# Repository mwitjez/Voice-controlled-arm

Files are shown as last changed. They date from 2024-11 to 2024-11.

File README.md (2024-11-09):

# Voice-Controlled Robotic Arm 🦾

## Project Overview

This project involves designing and constructing a robotic arm controlled via voice commands, utilizing Amazon Alexa for voice recognition. It explores key areas in robotics, including mechanical arm construction, voice control systems, and integration with various electronic components for seamless functionality. The goal is to create an intuitive robotic interface that allows users to interact naturally with the robot through simple commands.

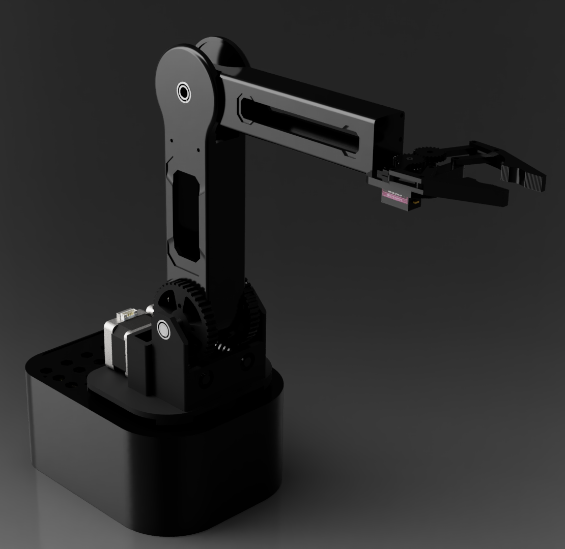
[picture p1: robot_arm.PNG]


## Table of Contents
- [Project Overview](#project-overview)
- [Project Objectives](#project-objectives)
- [Features](#features)
- [Technologies Used](#technologies-used)
- [System Architecture](#system-architecture)
- [Setup Instructions](#setup-instructions)
- [Usage](#usage)
- [Acknowledgments](#acknowledgments)

## Features

- **Voice Control**: The robotic arm can be controlled with voice commands, powered by Amazon Alexa.
- **Digital Control System**: Includes a custom PCB with an Arduino Nano and motor drivers to control stepper motors for precise movement.
- **Vision System**: Integrates a Microsoft Kinect camera for object detection and environmental awareness.
- **3D-Printed Components**: Many mechanical parts are 3D-printed, providing flexibility and accessibility in design.

## Technologies Used

- **Mechanical Design**: Autodesk Fusion 360, 3D Printing (PLA filament)
- **Electronics**: Arduino Nano, Raspberry Pi, TMC2130 Motor Drivers, Mean Well EDR-120-12 Power Supply
- **Programming Languages**: Python (for Raspberry Pi), C++ (for Arduino Nano)
- **Voice Assistant**: Amazon Alexa and AWS Lambda for command processing
- **Communication Protocols**: MQTT for communication between Raspberry Pi and Alexa's cloud services

## System Architecture

The system architecture consists of:
- **Voice Control Module**: Amazon Alexa interprets commands and communicates with the Raspberry Pi via AWS Lambda and MQTT.
- **Electronic Control Module**: A Raspberry Pi processes commands and interfaces with the Arduino Nano to control motors and the camera.
- **Mechanical Control Module**: Includes stepper motors and servo-based grippers for precise control of the robotic arm.

## Setup Instructions

### Project structure

```
.
├── 3D printed parts/   # 3D models for printed parts
├── code/               # Main application code
└── PCB/                # PCB design files
```

1. **Hardware Assembly**:
   - Assemble 3D-printed and off-the-shelf components, following the assembly guide.
   - Connect motors, camera, and power supply to the Raspberry Pi and Arduino Nano.
   
2. **Software Installation**:
   - Install the required Python libraries on Raspberry Pi for voice processing and motor control.
   - Set up the Arduino Nano with the control code for managing motor functions.
   - Configure the Alexa Skill with AWS Lambda function and enable MQTT for command messaging.

3. **Voice Command Setup**:
   - Configure the Alexa Skill for the robotic arm using the Alexa Skills Kit (ASK).
   - Link Alexa to the AWS IoT Core via MQTT for seamless communication.

## Usage

After setup, activate the Alexa skill with the command phrase `"Wake up, samurai"`, and use the following commands to control the robotic arm:
- **"Open the gripper"** or **"Close the gripper"**
- **"Move [direction] [distance]"** (e.g., "Move forward 5 centimeters")
- **"Rotate [direction] [angle]"** (e.g., "Rotate left 30 degrees")
- **"Pick it up"** - Grasp an object using the gripper
- **"Stop moving"** - Stop all movements

## Acknowledgments

This project was developed as part of an Engineering Thesis at Gdańsk University of Technology. All rights are reserved by the university.

Please note that the code and associated files for this project have not been updated and may be in an incomplete or outdated state. This project was initially developed four years ago, at a time when I had limited experience with the technologies and concepts involved. As a result, the structure and implementation may not reflect best practices or current standards. While the project serves as a foundation, it is recommended to consider it as a learning artifact rather than a fully polished, production-ready solution.

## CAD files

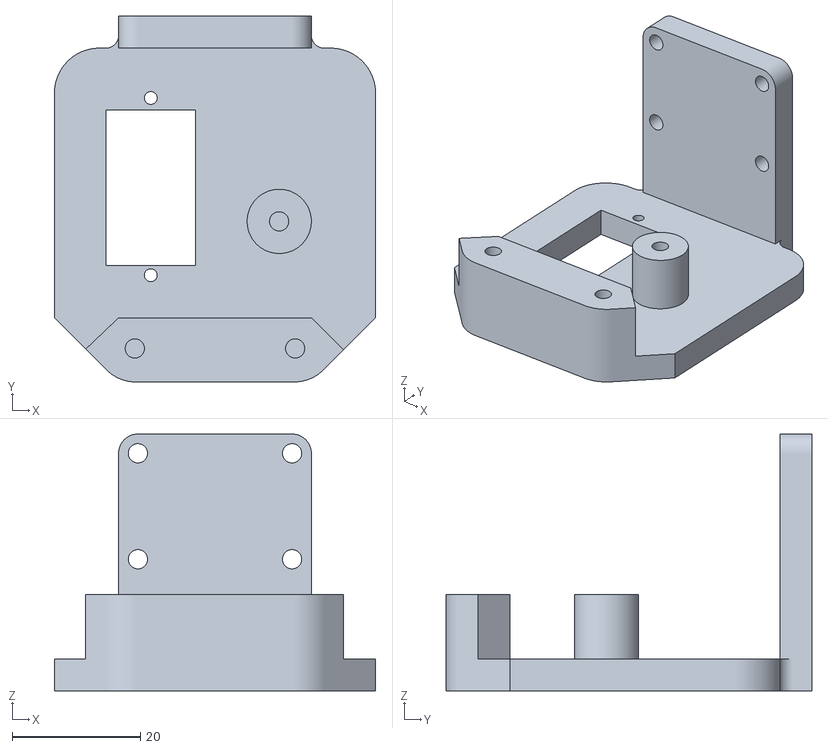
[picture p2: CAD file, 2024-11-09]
3D printed parts/Gripper base.stl
50.0 x 57.0 x 40.0

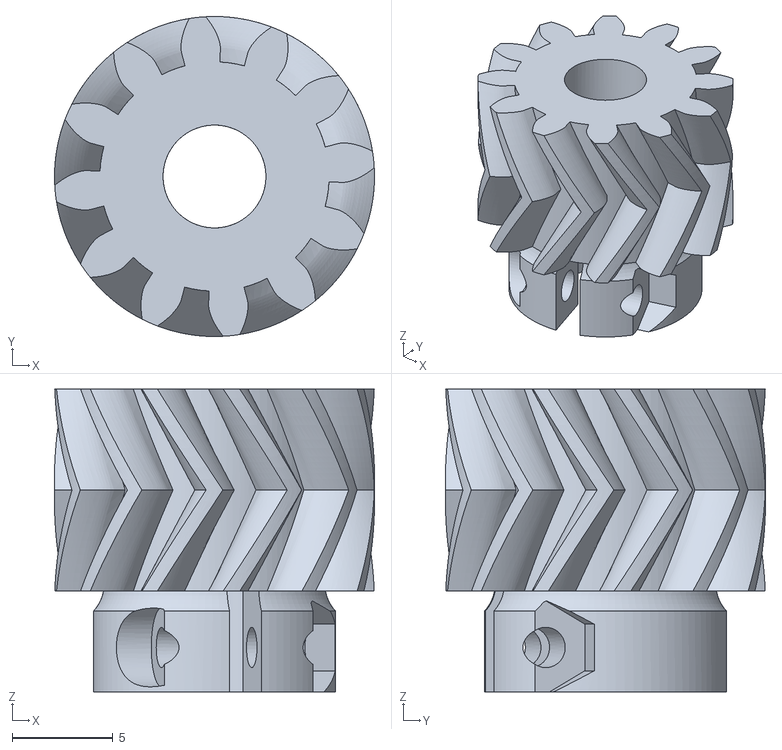
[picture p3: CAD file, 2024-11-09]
3D printed parts/Healical Gear base.stl
15.9 x 15.9 x 15.0

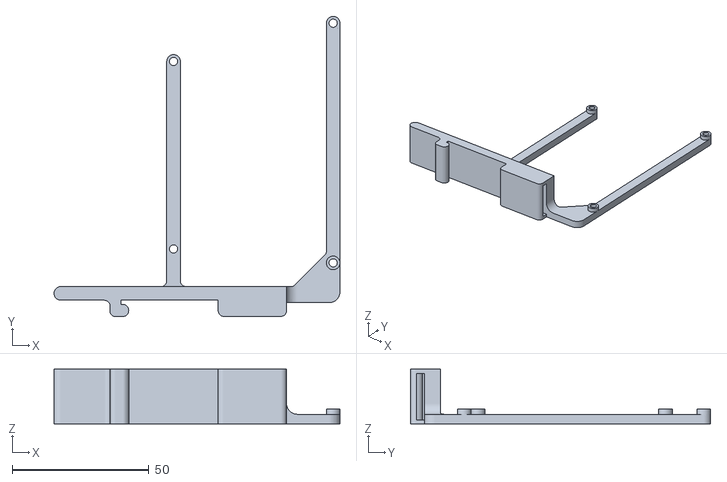
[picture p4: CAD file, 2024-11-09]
3D printed parts/PCB DIN mount.stl
104.5 x 109.7 x 20.0

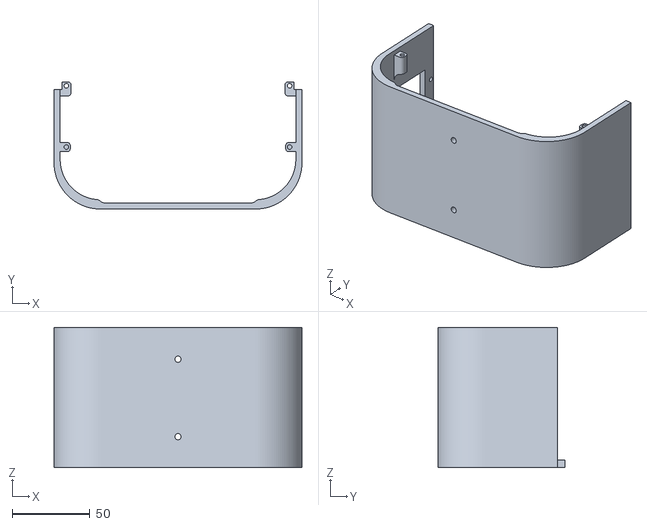
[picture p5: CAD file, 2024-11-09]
3D printed parts/Case back.stl
160.0 x 82.0 x 90.6

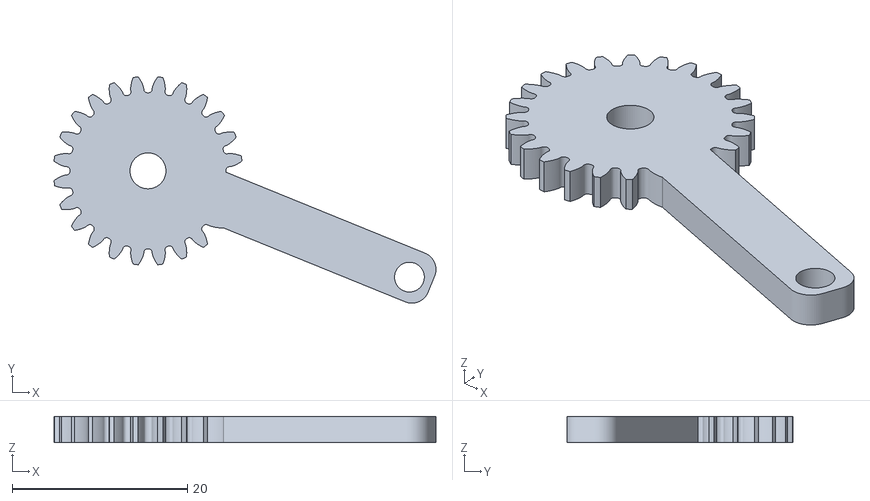
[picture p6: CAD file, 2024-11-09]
3D printed parts/gripper gear right.stl
43.6 x 25.8 x 3.00

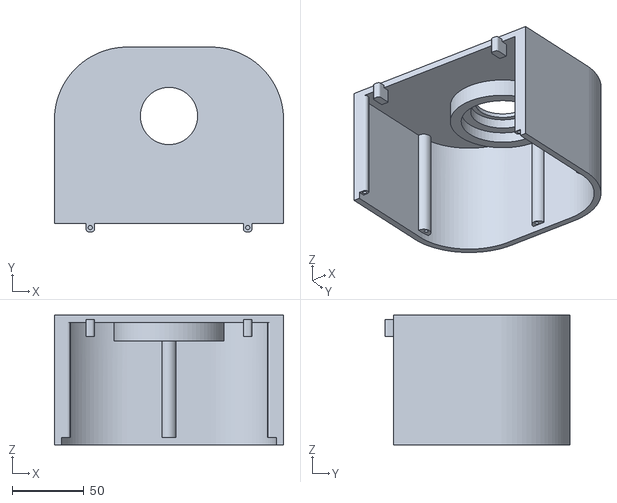
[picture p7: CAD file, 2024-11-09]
3D printed parts/Case front.stl
160.0 x 129.1 x 90.6

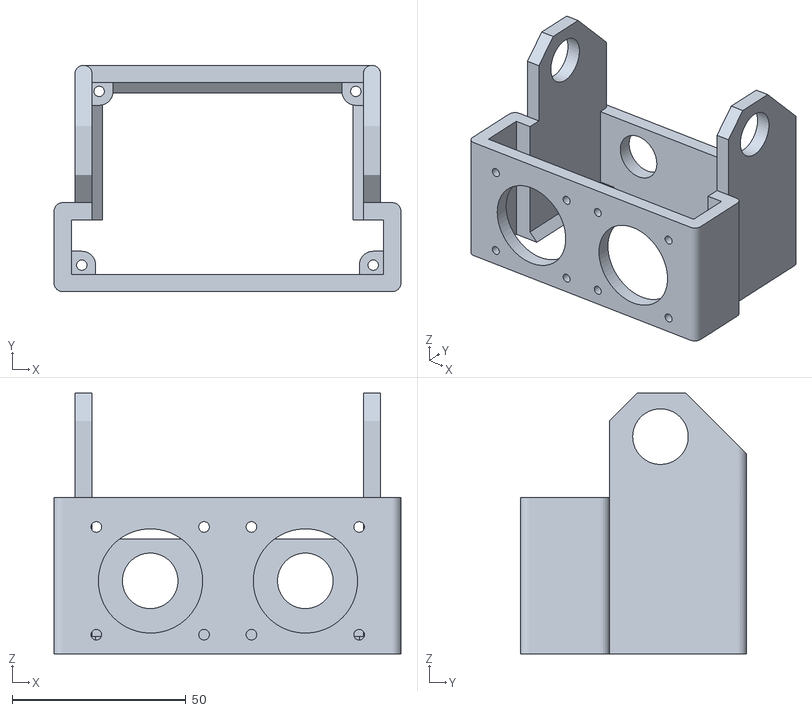
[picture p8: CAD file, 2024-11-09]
3D printed parts/Base upper.stl
99.9 x 65.1 x 75.0

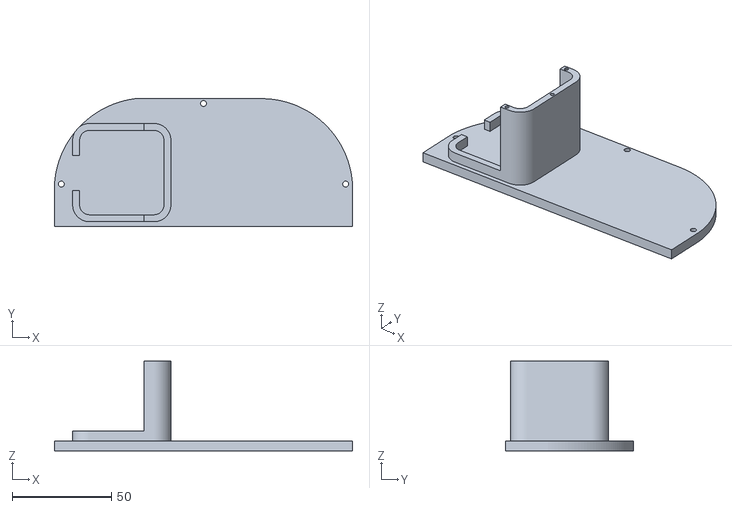
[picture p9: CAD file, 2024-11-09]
3D printed parts/Case lower.stl
149.8 x 64.2 x 45.0

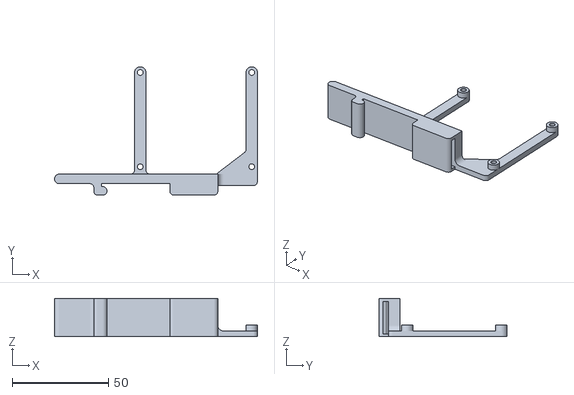
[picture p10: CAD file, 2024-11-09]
3D printed parts/rPi DIN mount.stl
105.6 x 66.8 x 20.0

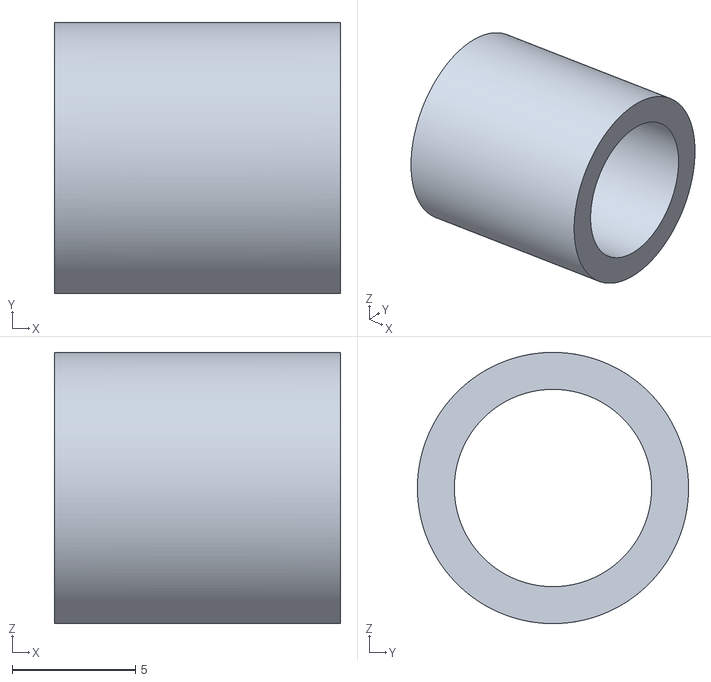
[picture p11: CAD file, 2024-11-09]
3D printed parts/spacer.stl
11.6 x 11.0 x 11.0

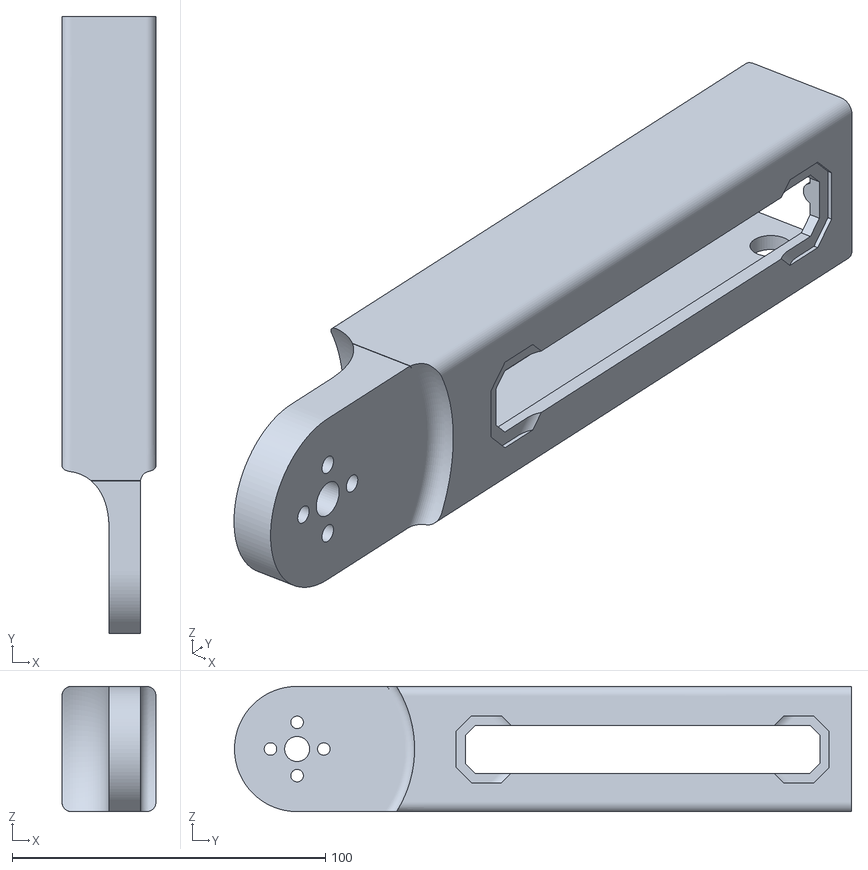
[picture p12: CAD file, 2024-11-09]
3D printed parts/Arm upper.stl
30.0 x 197.0 x 40.0

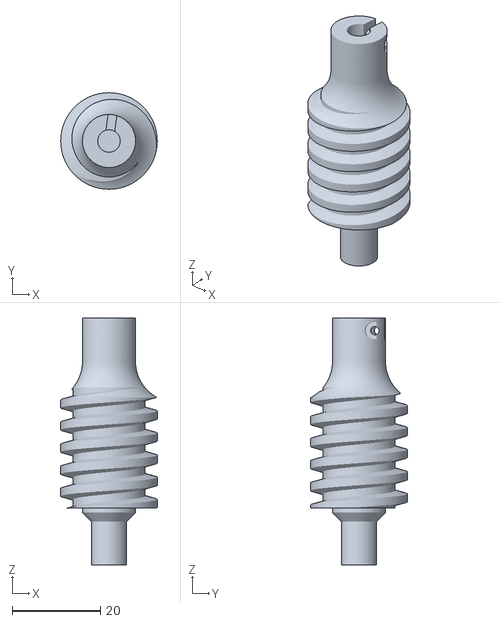
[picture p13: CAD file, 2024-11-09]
3D printed parts/worm upper fixed.stl
21.8 x 21.8 x 55.9

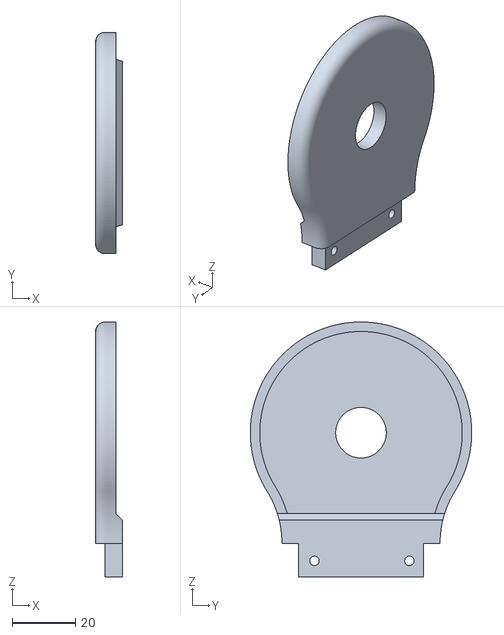
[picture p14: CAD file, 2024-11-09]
3D printed parts/Joint 2 connector.stl
8.50 x 70.0 x 80.6

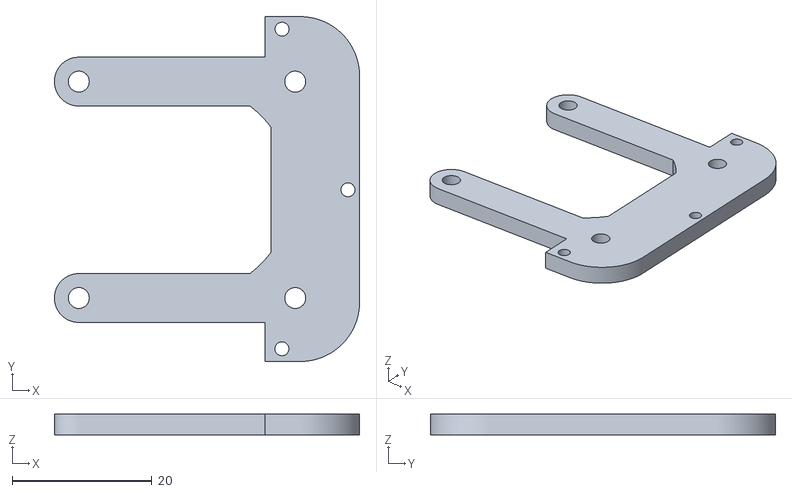
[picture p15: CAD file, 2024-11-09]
3D printed parts/Steper motor mount.stl
43.7 x 49.4 x 3.00

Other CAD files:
3D printed parts/worm wheel joint 2.stl
3D printed parts/worm wheel joint 1.stl
3D printed parts/Upper belt gear.stl
3D printed parts/Case cover.stl
3D printed parts/Base lower.stl
3D printed parts/gripper connector.stl
3D printed parts/gripper gear left.stl
3D printed parts/worm lower.stl

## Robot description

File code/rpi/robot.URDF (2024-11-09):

<?xml version="1.0" ?>

<robot name="samurai">

  <material name="Grey">
    <color rgba="0.2 0.2 0.2 1.0"/>
  </material>
  <material name="Orange">
    <color rgba="1.0 0.423529411765 0.0392156862745 1.0"/>
  </material>
  <material name="Blue">
  <color rgba="0.5 0.7 1.0 1.0"/>      
  </material>
  <material name="Red">
    <color rgba="1 0 0 1.0"/>      
  </material>

  <link name="base_link">
    <inertial>
      <origin rpy="0 0 0" xyz="0 0 0.273"/>
      <mass value="5"/>
      <inertia ixx="0.05" ixy="0" ixz="0" iyy="0.05" iyz="0" izz="0.05"/>
    </inertial>
    <visual>
      <origin rpy="0 0 0" xyz="0 0 0.273"/>
      <geometry>
        <cylinder radius="0.05" length="0.546"/>
      </geometry>
      <material name="Grey"/>
    </visual>
  </link>
  <!-- Joint 1 -->
  <joint name="Joint_1" type="revolute">
    <parent link="base_link"/>
    <child link="Link_1"/>
    <origin rpy="0 0 0" xyz="0 0 0.546"/>
    <axis xyz="0 0 1"/>
  </joint>
    <!-- Link 1 -->
  <link name="Link_1">
    <inertial>
      <origin rpy="0 0 0" xyz="0 0 0.5475"/>
      <mass value="5"/>
      <inertia ixx="0.05" ixy="0" ixz="0" iyy="0.05" iyz="0" izz="0.05"/>
    </inertial>
    <visual>
      <origin rpy="0 0 0" xyz="0 0 0.5475"/>
      <geometry>
        <cylinder radius="0.05" length="1.095"/>
      </geometry>
      <material name="Blue"/>
    </visual>
    <visual>
      <origin rpy="0 0 0" xyz="0 0 0"/>
      <geometry>
        <cylinder radius="0.1" length="0.1"/>
      </geometry>
      <material name="Orange"/>
    </visual>
  </link>
  <!-- Joint 2 -->
  <joint name="Joint_2" type="revolute">
    <parent link="Link_1"/>
    <child link="Link_2"/>
    <origin rpy="0 0 0" xyz="0 0 1.095"/>
    <axis xyz="1 0 0"/>
  </joint>
    <!-- Link 2 -->
  <link name="Link_2">
    <inertial>
      <origin rpy="0 0 0" xyz="0 0 0.805"/>
      <mass value="10"/>
      <inertia ixx="0.1" ixy="0" ixz="0" iyy="0.1" iyz="0" izz="0.1"/>
    </inertial>
    <visual>
      <origin rpy="0 0 0" xyz="0 0 0.805"/>
      <geometry>
        <cylinder radius="0.05" length="1.61"/>
      </geometry>
      <material name="Blue"/>
    </visual>
    <visual>
      <origin rpy="0 1.5708 0" xyz="0 0 0"/>
      <geometry>
        <cylinder radius="0.075" length="0.15"/>
      </geometry>
      <material name="Orange"/>
    </visual>
  </link>
  <!-- Joint 3 -->
  <joint name="Joint_3" type="revolute">
    <parent link="Link_2"/>
    <child link="Link_3"/>
    <origin rpy="0 0 0" xyz="0 0 1.61"/>
    <axis xyz="1 0 0"/>
  </joint>
    <!-- Link 3 -->
  <link name="Link_3">
    <inertial>
      <origin rpy="0 0 0" xyz="0 0 1.14"/>
      <mass value="10"/>
      <inertia ixx="0.1" ixy="0" ixz="0" iyy="0.1" iyz="0" izz="0.1"/>
    </inertial>
    <visual>
      <origin rpy="0 0 0" xyz="0 0 1.14"/>
      <geometry>
        <cylinder radius="0.05" length="2.28"/>
      </geometry>
      <material name="Blue"/>
    </visual>
    <visual>
      <origin rpy="0 1.5708 0" xyz="0 0 0"/>
      <geometry>
        <cylinder radius="0.075" length="0.15"/>
      </geometry>
      <material name="Orange"/>
    </visual>
  </link>
  <!-- Joint End-Effector -->
  <joint name="Joint_EE" type="fixed">
    <parent link="Link_3"/>
    <child link="Link_EE"/>
    <origin rpy="0 0 0" xyz="0 0 2.28"/>
    <axis xyz="1 0 0"/>
  </joint>
    <!-- End-Effector -->
  <link name="Link_EE">
    <inertial>
      <origin rpy="0 0 0" xyz="0 0 0"/>
      <mass value="0"/>
      <inertia ixx="0" ixy="0" ixz="0" iyy="0" iyz="0" izz="0"/>
    </inertial>
    <visual>
      <origin rpy="0 0 0" xyz="0 0 0"/>
      <geometry>
        <sphere radius="0.1"/>
      </geometry>
      <material name="Red"/>
    </visual>
  </link>
  
</robot>

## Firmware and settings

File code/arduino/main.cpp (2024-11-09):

#include <TMCStepper.h>
#include <AccelStepper.h>
#include <Servo.h>
#include <Arduino.h>

#define DIR_BASE_PIN 9     // Direction
#define STEP_BASE_PIN 8    // Step
#define DIR_JOINT1_PIN A1  // Direction
#define STEP_JOINT1_PIN A0 // Step
#define DIR_JOINT2_PIN A3  // Direction
#define STEP_JOINT2_PIN A2 // Step
#define CS_BASE_PIN 10     // Chip select mottor base
#define CS_JOINT1_PIN 7    // Chip select mottor joint 1
#define CS_JOINT2_PIN 4    // Chip select mottor joint 1
#define SW_MOSI 11         // Software Master Out Slave In (MOSI)
#define SW_MISO 12         // Software Master In Slave Out (MISO)
#define SW_SCK 13          // Software Slave Clock (SCK)
#define SERVO_PIN 3

#define R_SENSE 0.11f // Match to your driver- SilentStepStick series use 0.11

// Select your stepper driver type
TMC2130Stepper driver_base = TMC2130Stepper(CS_BASE_PIN, R_SENSE);     // Hardware SPI
TMC2130Stepper driver_joint1 = TMC2130Stepper(CS_JOINT1_PIN, R_SENSE); // Hardware SPI
TMC2130Stepper driver_joint2 = TMC2130Stepper(CS_JOINT2_PIN, R_SENSE); // Hardware SPI

constexpr uint32_t steps_per_mm = 80;

AccelStepper stepper_base = AccelStepper(stepper_base.DRIVER, STEP_BASE_PIN, DIR_BASE_PIN);
AccelStepper stepper_joint1 = AccelStepper(stepper_joint1.DRIVER, STEP_JOINT1_PIN, DIR_JOINT1_PIN);
AccelStepper stepper_joint2 = AccelStepper(stepper_joint2.DRIVER, STEP_JOINT2_PIN, DIR_JOINT2_PIN);

Servo servo_gripper;
int servo_start_pos;
int servo_pos;

String msg;

void close_gripper()
{
  for (servo_pos = 0; servo_pos <= 50; servo_pos += 1)
  {                                 // goes from 0 degrees to 50 degrees
    servo_gripper.write(servo_pos); // tell servo to go to position in variable 'pos'
    delay(15);                      // waits 15 ms for the servo to reach the position
  }
}

void open_gripper()
{
  Serial.println("Opening..");
  for (servo_pos = 50; servo_pos >= 0; servo_pos -= 1)
  {                                 // goes from 0 degrees to 50 degrees
    servo_gripper.write(servo_pos); // tell servo to go to position in variable 'pos'
    delay(15);                      // waits 15 ms for the servo to reach the position
  }
}

void rotate_base(int degrees, String dir)
// 44.44 =  5*16*200/360
// 5 - przełożenie
// 16 - rozdzielczość mikrokroków
// 200 - podstawowa rozdzielczość silnika
{
  if (dir == "right")
  {
    stepper_base.move(-degrees * 44.44);
  }
  else
  {
    stepper_base.move(degrees * 44.44);
  }
  stepper_base.runToPosition();
}

void move_joint1(int degrees)
{
  // 355.55 =  5*16*200/360
  // 40 - przełożenie
  // 16 - rozdzielczość mikrokroków
  // 200 - podstawowa rozdzielczość silnika
  stepper_joint1.move(degrees * 355.55);
  stepper_joint1.runToPosition();
}

void move_joint2(int degrees)
{
  // 853.33 =  5*16*200/360
  // 2.4*40 - przełożenie
  // 16 - rozdzielczość mikrokroków
  // 200 - podstawowa rozdzielczość silnika
  stepper_joint2.move(degrees * 853.33);
  stepper_joint2.runToPosition();
}

void readSerialPort()
{
  msg = "";
  if (Serial.available())
  {
    delay(10);
    while (Serial.available() > 0)
    {
      msg += (char)Serial.read();
    }
    Serial.flush();
  }
}

void setup()
{
  SPI.begin();
  Serial.begin(9600);
  while (!Serial)
    ;
  Serial.println("Start...");

  // konfiguracja pierwszego sterownika
  pinMode(CS_BASE_PIN, OUTPUT);
  digitalWrite(CS_BASE_PIN, HIGH);
  driver_base.begin();          // Initiate pins and registeries
  driver_base.rms_current(600); // Set stepper current to 600mA. The command is the same as command TMC2130.setCurrent(600, 0.11, 0.5);
  driver_base.en_pwm_mode(1);   // Enable extremely quiet stepping
  driver_base.pwm_autoscale(1);
  driver_base.microsteps(16);

  stepper_base.setMaxSpeed(50 * steps_per_mm);      // 100mm/s @ 80 steps/mm
  stepper_base.setAcceleration(500 * steps_per_mm); // 2000mm/s^2
  stepper_base.setPinsInverted(false, false, true);
  stepper_base.enableOutputs();
  digitalWrite(CS_BASE_PIN, LOW);
  // konfiguracja drugiego sterownika
  pinMode(CS_JOINT1_PIN, OUTPUT);
  digitalWrite(CS_JOINT1_PIN, HIGH);
  driver_joint1.begin();          // Initiate pins and registeries
  driver_joint1.rms_current(600); // Set stepper current to 600mA. The command is the same as command TMC2130.setCurrent(600, 0.11, 0.5);
  driver_joint1.en_pwm_mode(1);   // Enable extremely quiet stepping
  driver_joint1.pwm_autoscale(1);
  driver_joint1.microsteps(16);

  stepper_joint1.setMaxSpeed(100 * steps_per_mm);     // 100mm/s @ 80 steps/mm
  stepper_joint1.setAcceleration(500 * steps_per_mm); // 2000mm/s^2
  stepper_joint1.setPinsInverted(false, false, true);
  stepper_joint1.enableOutputs();
  digitalWrite(CS_JOINT1_PIN, LOW);
  // konfiguracja trzeciego sterownika
  pinMode(CS_JOINT2_PIN, OUTPUT);
  digitalWrite(CS_JOINT2_PIN, HIGH);
  driver_joint2.begin();          // Initiate pins and registeries
  driver_joint2.rms_current(600); // Set stepper current to 600mA. The command is the same as command TMC2130.setCurrent(600, 0.11, 0.5);
  driver_joint2.en_pwm_mode(1);   // Enable extremely quiet stepping
  driver_joint2.pwm_autoscale(1);
  driver_joint2.microsteps(16);

  stepper_joint2.setMaxSpeed(50 * steps_per_mm);       // 100mm/s @ 80 steps/mm
  stepper_joint2.setAcceleration(1000 * steps_per_mm); // 2000mm/s^2
  stepper_joint2.setPinsInverted(false, false, true);
  stepper_joint2.enableOutputs();
  digitalWrite(CS_JOINT2_PIN, LOW);

  // konfiguracja serwomechanizmu
  servo_gripper.write(0);
  servo_gripper.attach(SERVO_PIN);
  servo_start_pos = servo_gripper.read();
}

void loop()
{
  readSerialPort();
  if (msg == "open")
  {
    open_gripper();
    Serial.println("Opening...");
  }
  else if (msg == "close")
  {
    close_gripper();
    Serial.println("Closing...");
  }
  else if (msg == "stop")
  {
    stepper_base.stop();
    stepper_joint1.stop();
    stepper_joint2.stop();
    Serial.println("Stoping..");
  }
  else if (msg.startsWith("rotate"))
  {
    int degrees = msg.substring(6, 8).toInt();
    String direction = msg.substring(8);
    Serial.println("Moving...");
    rotate_base(degrees, direction);
  }
  else if (msg.startsWith("move_joint1"))
  {
    int degrees = msg.substring(11).toFloat();
    Serial.println("Moving joint1...");
    Serial.println(degrees);
    move_joint1(degrees);
  }
  else if (msg.startsWith("move_joint2"))
  {
    int degrees = msg.substring(11).toFloat();
    Serial.println("Moving joint2...");
    Serial.println(degrees);
    move_joint2(degrees);
  }
  else if (msg != "")
  {
    Serial.println("Unknown message: ");
    Serial.println(msg);
  }
  delay(500);
}

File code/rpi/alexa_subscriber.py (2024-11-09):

import json
import time
from awscrt import io, mqtt, auth, http
from awsiot import mqtt_connection_builder
import sys
from uuid import uuid4
import serial
import ikpy.chain
import numpy as np
import freenect
import cv2
import json

endpoint = ""
port = 8883
root_ca = "AmazonRootCA1.pem"
key = ""
cert = ""
client_id = "pi-" + str(uuid4())
topic = "voice"

robot_chain = ikpy.chain.Chain.from_urdf_file("robot.URDF")
current_orientation = [0, 0, 0, np.deg2rad(90), 0]
current_pos = robot_chain.forward_kinematics(current_orientation)[:3, 3]


def get_video():
    array, _ = freenect.sync_get_video()
    array = cv2.cvtColor(array, cv2.COLOR_RGB2BGR)
    return array


def get_depth():
    array, _ = freenect.sync_get_depth()
    array = array.astype(np.uint8)
    return array


# Callback when connection is accidentally lost.
def on_connection_interrupted(connection, error, **kwargs):
    print("Connection interrupted. error: {}".format(error))


# Callback when an interrupted connection is re-established.
def on_connection_resumed(connection, return_code, session_present, **kwargs):
    print("Connection resumed. return_code: {} session_present: {}".format(
        return_code, session_present))

    if return_code == mqtt.ConnectReturnCode.ACCEPTED and not session_present:
        print("Session did not persist. Resubscribing to existing topics...")
        resubscribe_future, _ = connection.resubscribe_existing_topics()

        # Cannot synchronously wait for resubscribe result because we're on the connection's event-loop thread,
        # evaluate result with a callback instead.
        resubscribe_future.add_done_callback(on_resubscribe_complete)


def calculate_angles(movement_value, direction):
    # funkcja oblicza kąty robota na podstawie zadanej pozycji
    global current_orientation
    if direction == "up":
        target_pos = [
            current_pos[0], current_pos[1], current_pos[2] + movement_value
        ]
        target_orentation = robot_chain.inverse_kinematics(target_pos)
    elif direction == "down":
        target_pos = [
            current_pos[0], current_pos[1], current_pos[2] - movement_value
        ]
        target_orentation = robot_chain.inverse_kinematics(target_pos)
    elif direction == "forward" or direction == "forwards":
        target_pos = [
            current_pos[0], current_pos[1] - movement_value, current_pos[2]
        ]
        target_orentation = robot_chain.inverse_kinematics(target_pos)
    elif direction == "backward" or direction == "backwards":
        target_pos = [
            current_pos[0], current_pos[1] + movement_value, current_pos[2]
        ]
        target_orentation = robot_chain.inverse_kinematics(target_pos)

    previous_orientation = current_orientation
    current_orientation = target_orentation
    return target_pos, previous_orientation


def open_action():
    cmd = "open"
    arduino.write(cmd.encode())
    print("opening...")


def close_action():
    cmd = "close"
    arduino.write(cmd.encode())
    print("closing...")


def stop_action():
    cmd = "stop"
    arduino.write(cmd.encode())
    print("stoping...")


def move_base_action(degrees, direction):
    cmd = "rotate" + str(degrees) + str(direction)
    arduino.write(cmd.encode())
    print("moving...")


def move_arm_action(value, direction):
    global current_orientation, current_pos
    value = float(value) / 10
    target_pos, previous_orientation = calculate_angles(value, direction)
    current_pos = robot_chain.forward_kinematics(current_orientation)[:3, 3]
    print(np.rad2deg(current_orientation))
    # czy kąty robota nie są przekraczane (robot nie wjedzie sam w siebie)
    # czy punkt jest w zasięgu robota z przybliżeniem do 4 miejsca po przecinku
    if np.rad2deg(current_orientation[2]) < 85 and np.rad2deg(
            current_orientation[2]) > -30 and np.rad2deg(
                current_orientation[3]) < 130 and np.rad2deg(
                    current_orientation[3]) > -90 and np.all(
                        np.isclose(current_pos,
                                   target_pos,
                                   rtol=1e-04,
                                   atol=1e-04,
                                   equal_nan=False)):

        angle_joint1 = np.rad2deg(previous_orientation[2] -
                                  current_orientation[2])
        angle_joint2 = np.rad2deg(previous_orientation[3] -
                                  current_orientation[3])

        print(angle_joint1)
        print(angle_joint2)
        cmd_joint1 = "move_joint1" + str(int(round(angle_joint1)))
        arduino.write(cmd_joint1.encode())
        time.sleep(0.8)
        cmd_joint2 = "move_joint2" + str(int(round(angle_joint2)))
        arduino.write(cmd_joint2.encode())
        print("moving...")
    else:
        print("Wrong angle or can't reach position")

        print(np.rad2deg(current_orientation))
        angle_joint1 = np.rad2deg(previous_orientation[2] -
                                  current_orientation[2])
        angle_joint2 = np.rad2deg(previous_orientation[3] -
                                  current_orientation[3])

        print(angle_joint1)
        print(angle_joint2)
        # powrót do poprzedniej pozycji w przypadku zbyt dużej wartości kąta
        current_orientation = previous_orientation
        current_pos = robot_chain.forward_kinematics(current_orientation)[:3,
                                                                          3]


def getContours(img, imgResult):
    contours, hierarchy = cv2.findContours(img, cv2.RETR_EXTERNAL,
                                           cv2.CHAIN_APPROX_NONE)
    x, y, w, h = 0, 0, 0, 0
    for countour in contours:
        area = cv2.contourArea(countour)
        if area > 70:
            cv2.drawContours(imgResult, countour, -1, (255, 0, 0), 3)
            peri = cv2.arcLength(countour, True)
            approx = cv2.approxPolyDP(countour, 0.02 * peri, True)
            x, y, w, h = cv2.boundingRect(approx)
    return x + w // 2, y, imgResult


def get_depth_to_obj(depth, x_pos, y_pos):
    sum_depth = 0
    number_of_samples = 0
    area_size = 2  # wiekośc obszaru przeszukiwania
    for x in range(x_pos - area_size, x_pos + area_size):
        for y in range(y_pos - area_size, y_pos + area_size):
            point_depth = depth[y, x]
            if point_depth != 255:
                sum_depth += point_depth
                number_of_samples += 1
            print(point_depth)

    if number_of_samples != 0:
        avg_depth = sum_depth / number_of_samples
    else:
        avg_depth = -1
    return avg_depth
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
